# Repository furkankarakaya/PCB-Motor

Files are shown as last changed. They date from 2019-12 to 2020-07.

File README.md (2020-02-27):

# PCB-Motor

* Nominal speed: 2000 RPM

* Nominal torque: 180 mN.m

* Nominal output power: 38 W

* Pole: 16

* Frequency: 266.67 Hz

* Iphase: 2 Arms

* Core width: 5 mm

* Core inner diameter: 50 mm

* Core outer diameter: 92 mm

* Magnet width: 2 mm

* Air gap: 1 mm

* PCB width: 1 mm

* PCB inner diameter: 50 mm

* PCB outer diameter: 98 mm

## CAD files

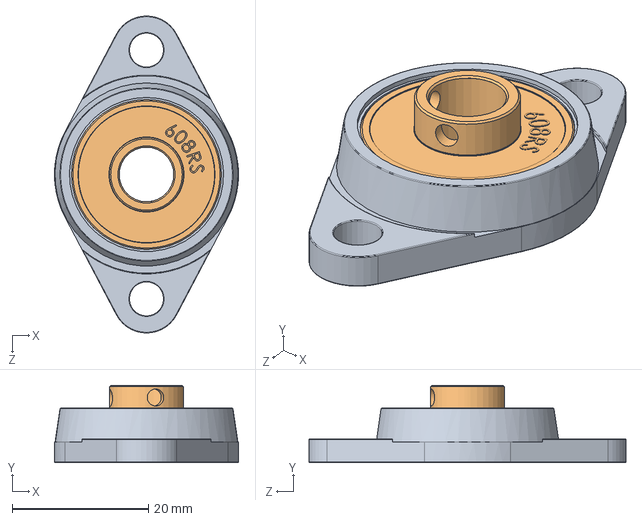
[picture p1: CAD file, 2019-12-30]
mechanical model/ufl-serisi-yatakli-rulman-ufl-series-bearing-1.snapshot.3/KFL08.SLDASM
27.0 x 11.4 x 46.5 mm
KFL08
608RS

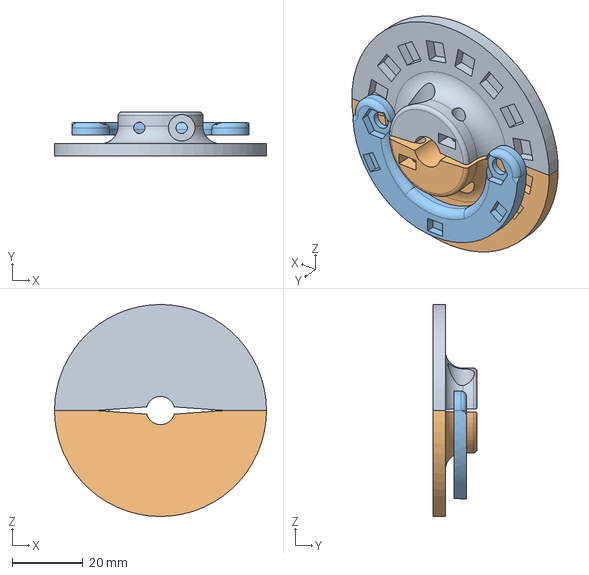
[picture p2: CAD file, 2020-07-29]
mechanical model/hall sensor assembly/PCBmotor-HallSensor.stp
60.0 x 12.5 x 60.0 mm

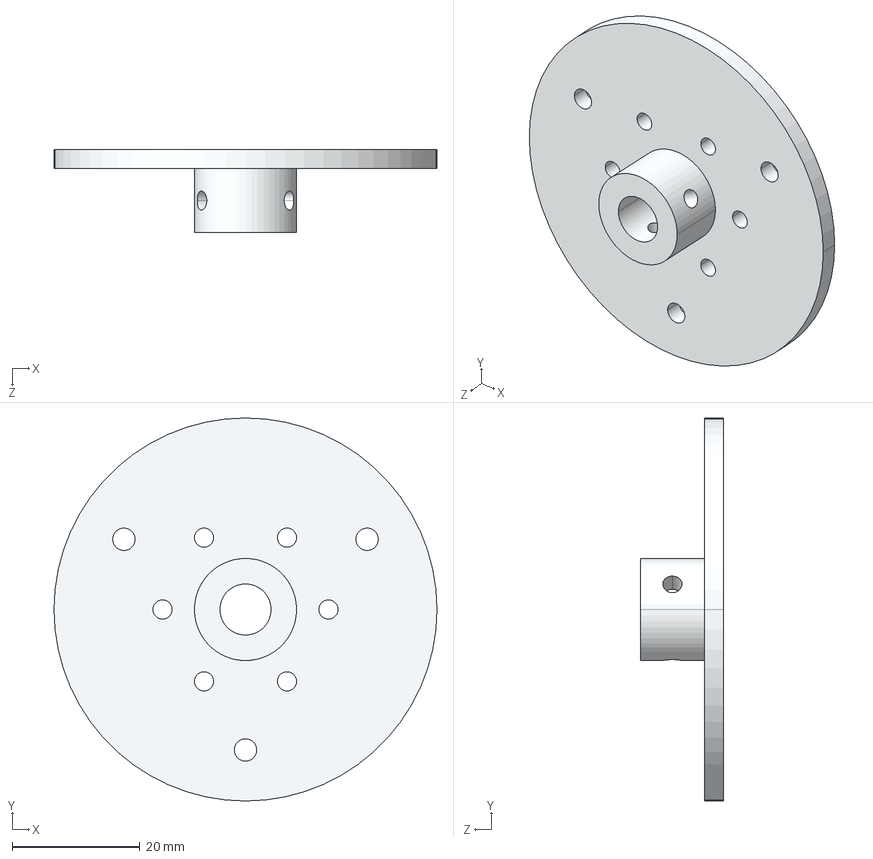
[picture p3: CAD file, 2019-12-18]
mechanical model/üretim/yeni_kapak.STEP
60.0 x 60.0 x 13.0 mm

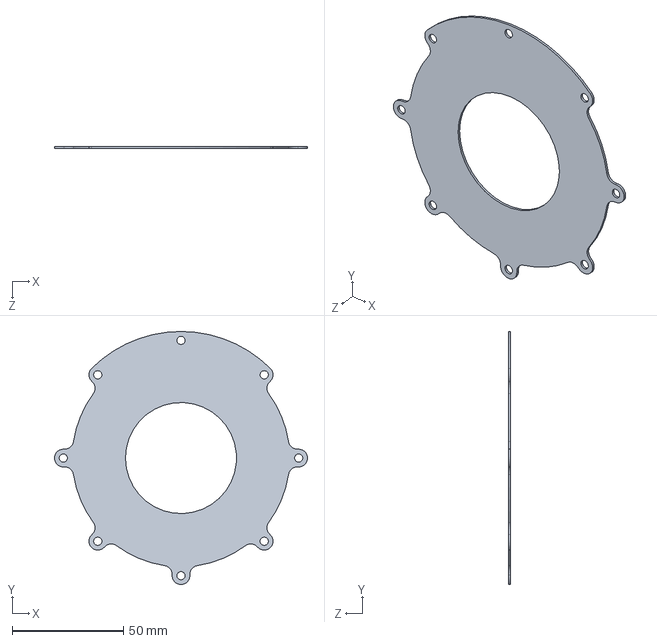
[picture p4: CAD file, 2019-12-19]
pcb/mechanical outline/outline.SLDPRT
113.9 x 114.0 x 1.00 mm

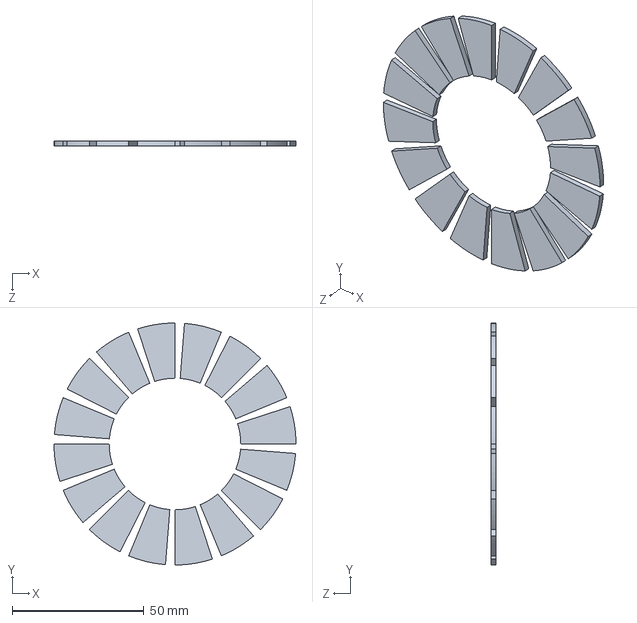
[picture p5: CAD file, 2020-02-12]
mechanical model/Magnets.SLDPRT
92.0 x 92.0 x 2.00 mm

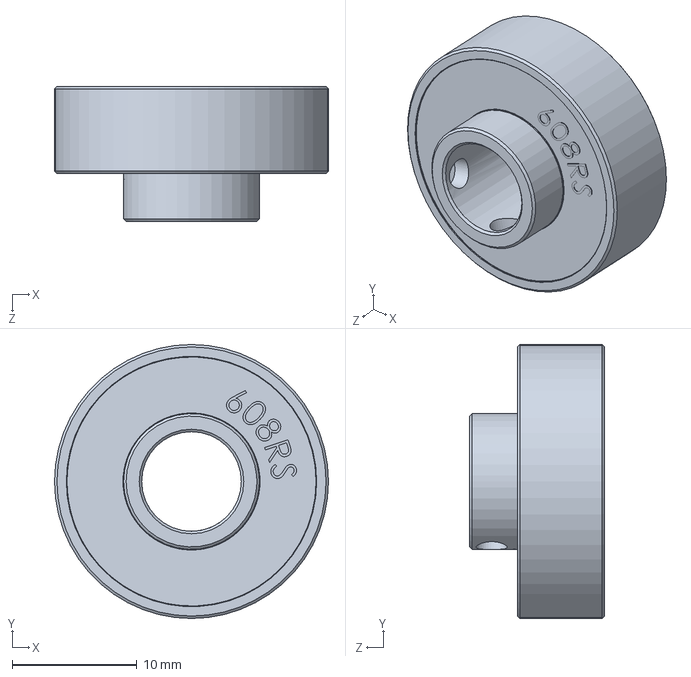
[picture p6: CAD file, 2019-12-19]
mechanical model/ufl-serisi-yatakli-rulman-ufl-series-bearing-1.snapshot.3/608RS.SLDPRT
22.0 x 22.0 x 10.9 mm

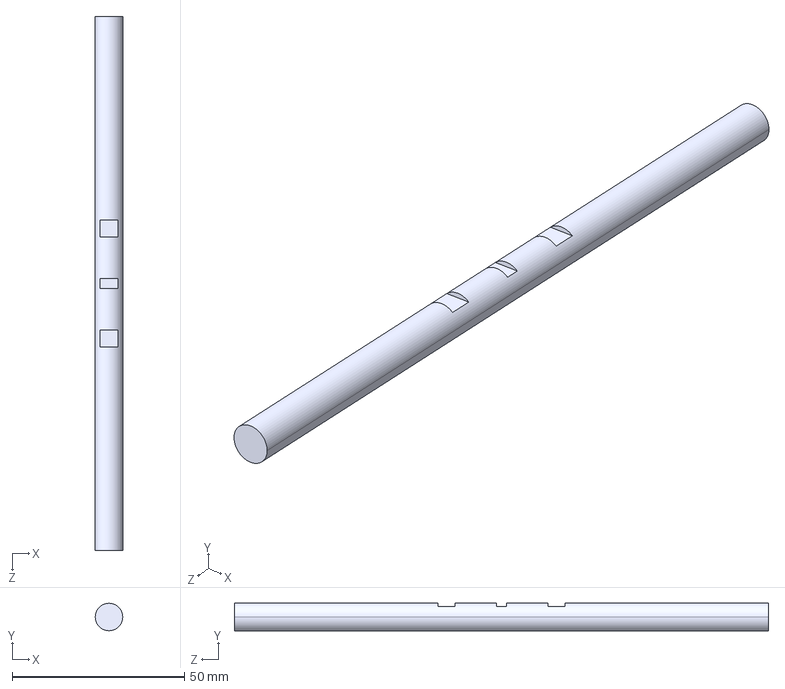
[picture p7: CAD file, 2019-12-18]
mechanical model/üretim/yeni_mil.STEP
8.00 x 8.00 x 155.0 mm

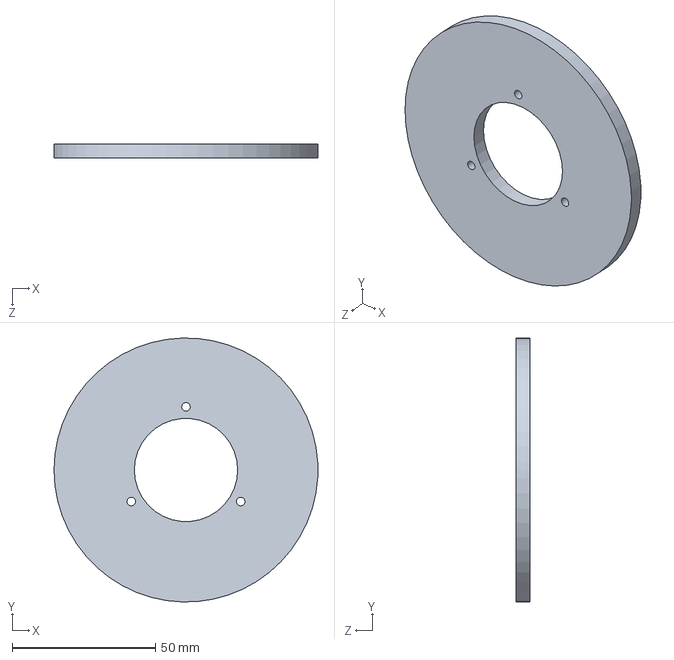
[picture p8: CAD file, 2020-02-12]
mechanical model/rotor.SLDPRT
92.0 x 92.0 x 5.00 mm

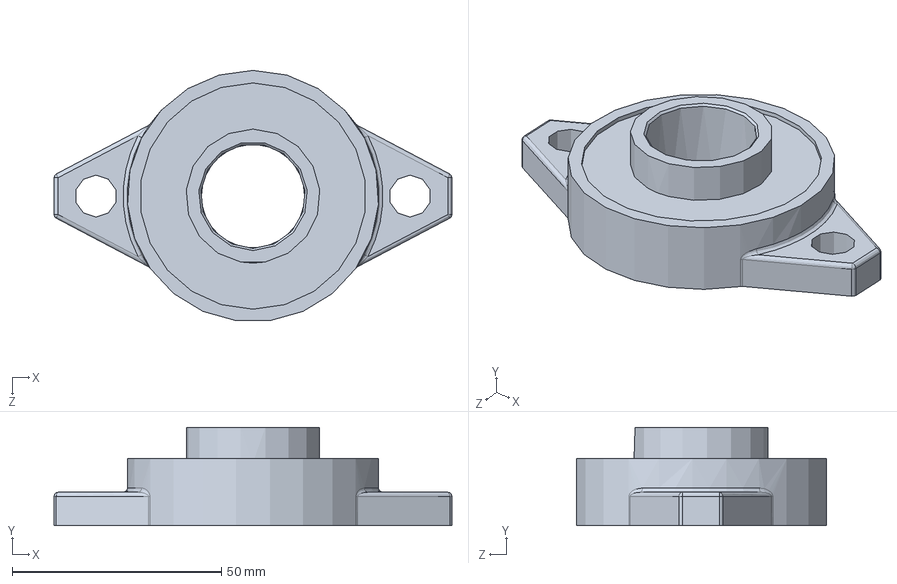
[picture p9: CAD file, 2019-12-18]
mechanical model/ufl-serisi-yatakli-rulman-ufl-series-bearing-1.snapshot.3/Yatakli Rulman UFL.SLDPRT
95.0 x 23.5 x 59.7 mm

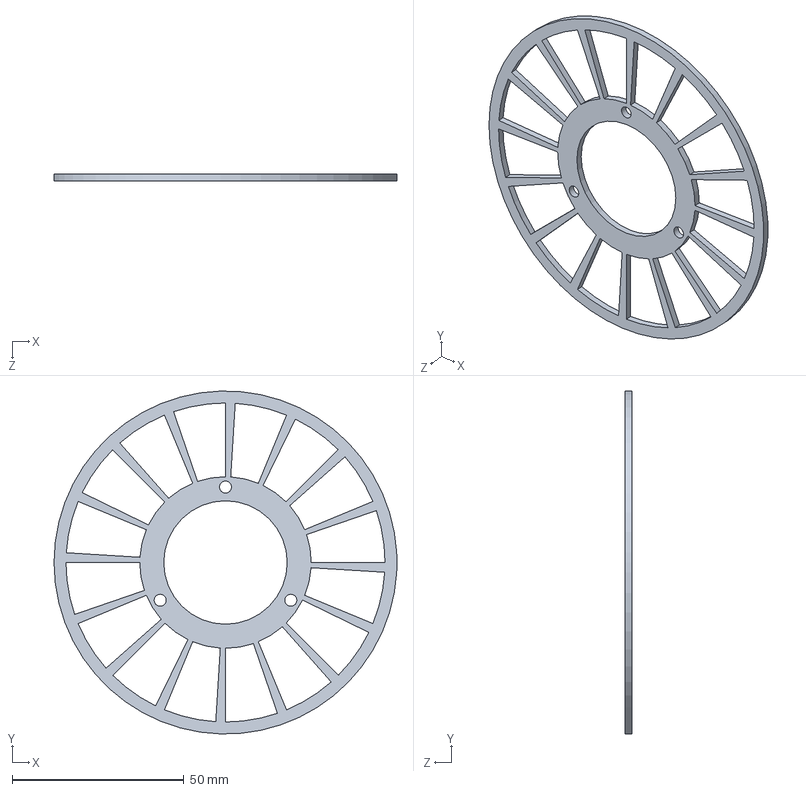
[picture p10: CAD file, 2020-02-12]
mechanical model/magnet tutucu.SLDPRT
100.0 x 100.0 x 2.00 mm

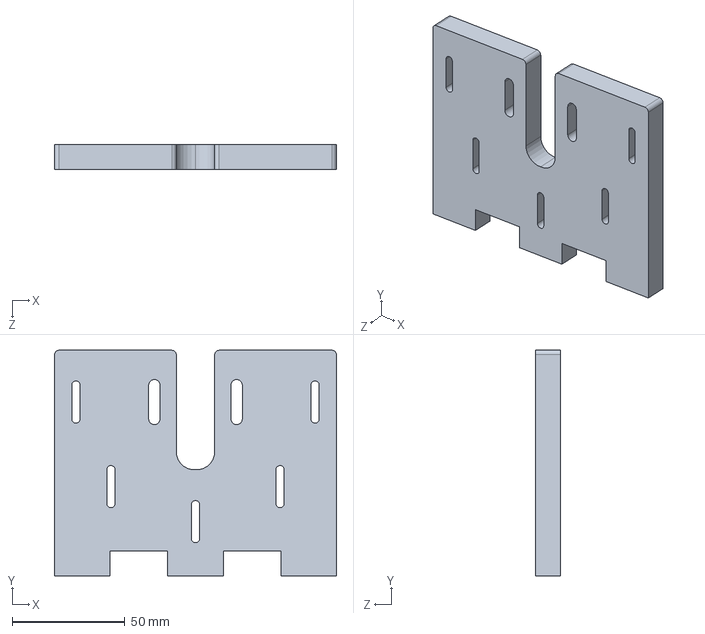
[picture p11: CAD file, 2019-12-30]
mechanical model/yan_destek.SLDPRT
125.0 x 100.0 x 11.0 mm

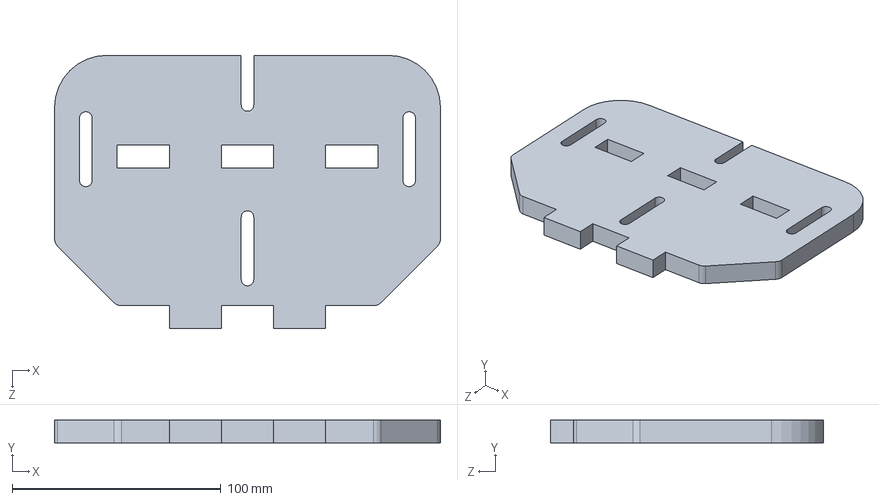
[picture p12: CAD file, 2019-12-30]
mechanical model/alt_destek.SLDPRT
185.0 x 11.0 x 131.0 mm

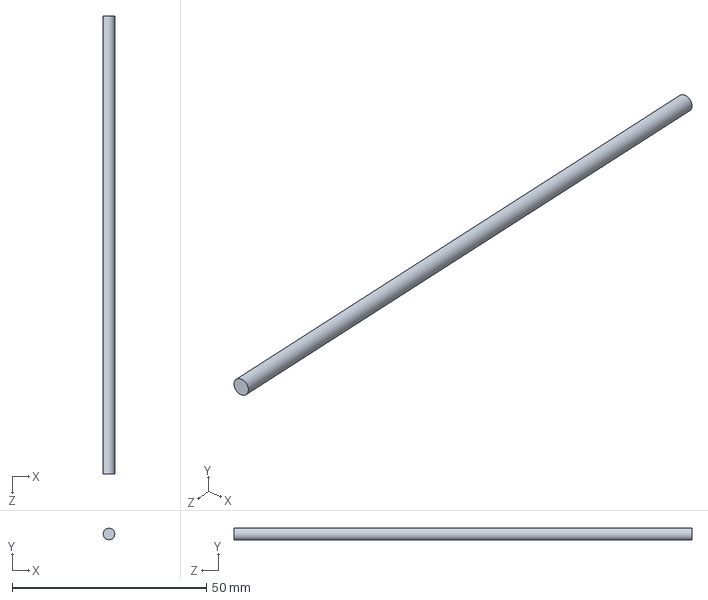
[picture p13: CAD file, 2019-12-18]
mechanical model/saplama.SLDPRT
3.00 x 3.00 x 118.0 mm

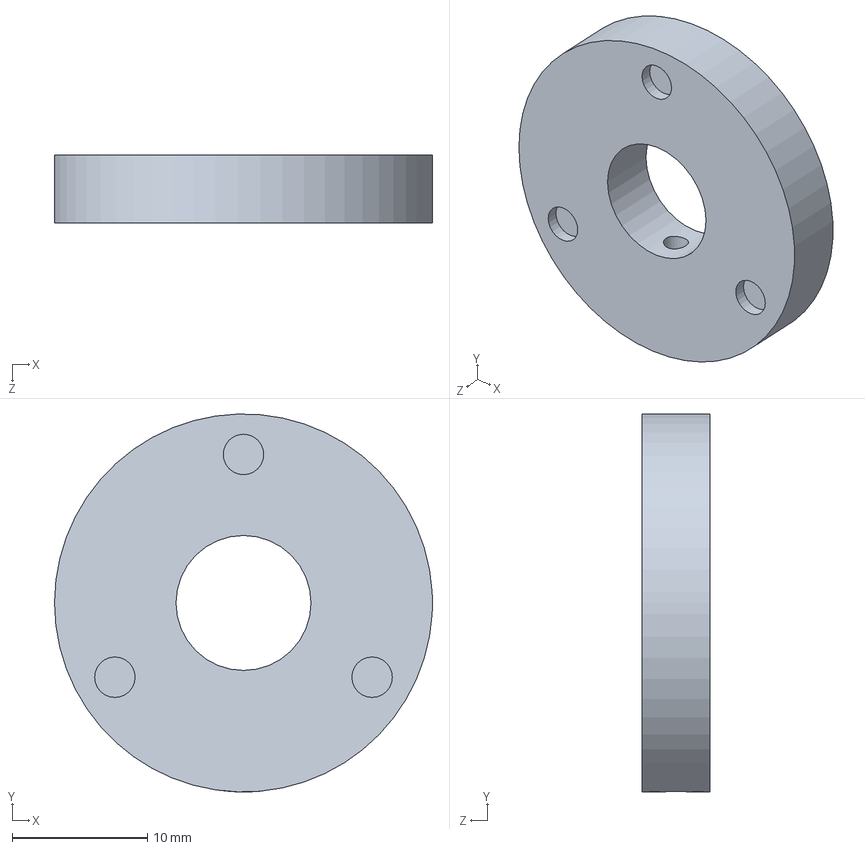
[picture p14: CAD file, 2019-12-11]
mechanical model/dayanak.SLDPRT
28.0 x 28.0 x 5.00 mm

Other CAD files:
mechanical model/wave_winding.SLDPRT
mechanical model/üretim/rotor.STEP
mechanical model/mil.SLDPRT
mechanical model/kapak.SLDPRT
mechanical model/hall sensor assembly/PCBmotor-HallSensor.f3d
mechanical model/hall sensor assembly/PCBmotor-HallSensor.stl
mechanical model/pcb.SLDPRT
mechanical model/rotor-kaburgali.SLDPRT
mechanical model/ufl-serisi-yatakli-rulman-ufl-series-bearing-1.snapshot.3/KFL08.SLDPRT
mechanical model/üretim/rotor.SLDDRW

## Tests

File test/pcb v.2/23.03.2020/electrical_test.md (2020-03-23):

# Electrical test of the PCB
## Concentric Winding
### Phase A
- 1.07 Ohm
- 10.4 uH

### Phase B
- 1.07 Ohm
- 10.4 uH

### Phase C
- 1.07 Ohm
- 10.4 uH

## Parallel Winding
### Phase A
- 789 mOhm
- 3.15 uH

### Phase B
- 787 mOhm
- 3.13 uH

### Phase C
- 806 mOhm
- 3.17 uH

## ARC Winding
### Phase A
- 896 mOhm
- 3.34 uH

### Phase B
- 894 mOhm
- 3.34 uH

### Phase C
- 914 mOhm
- 3.35 uH

## UEW Winding
### Phase A
- 661 mOhm
- 3 uH

### Phase B
- 661 mOhm
- 3 uH

### Phase C
- 679 mOhm
- 3.05 uH

## Radial Winding
### Phase A
- 860 mOhm
- 4 uH

### Phase B
- 859 mOhm
- 4 uH

### Phase C
- 877 mOhm
- 4 uH

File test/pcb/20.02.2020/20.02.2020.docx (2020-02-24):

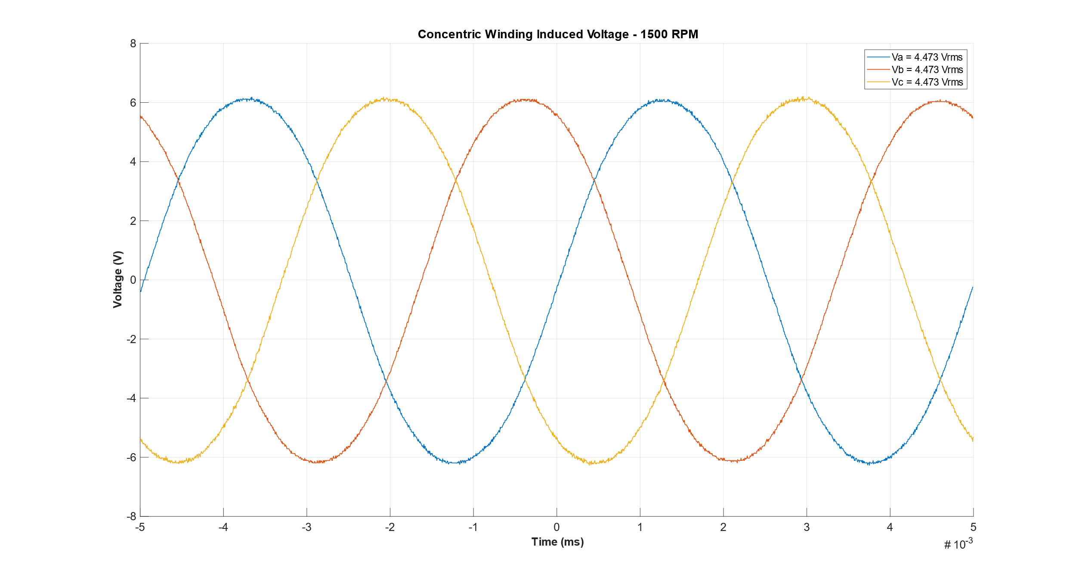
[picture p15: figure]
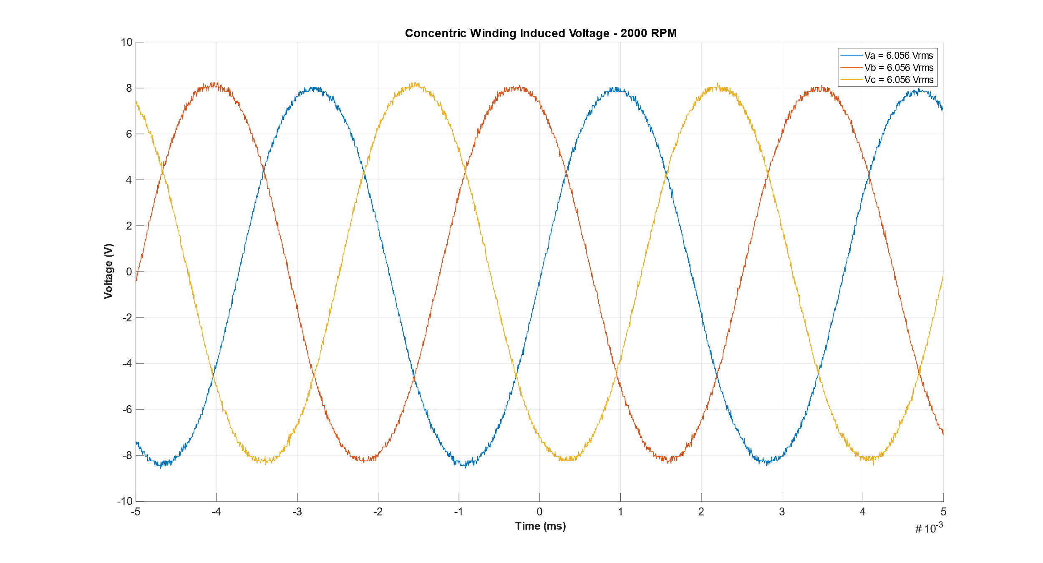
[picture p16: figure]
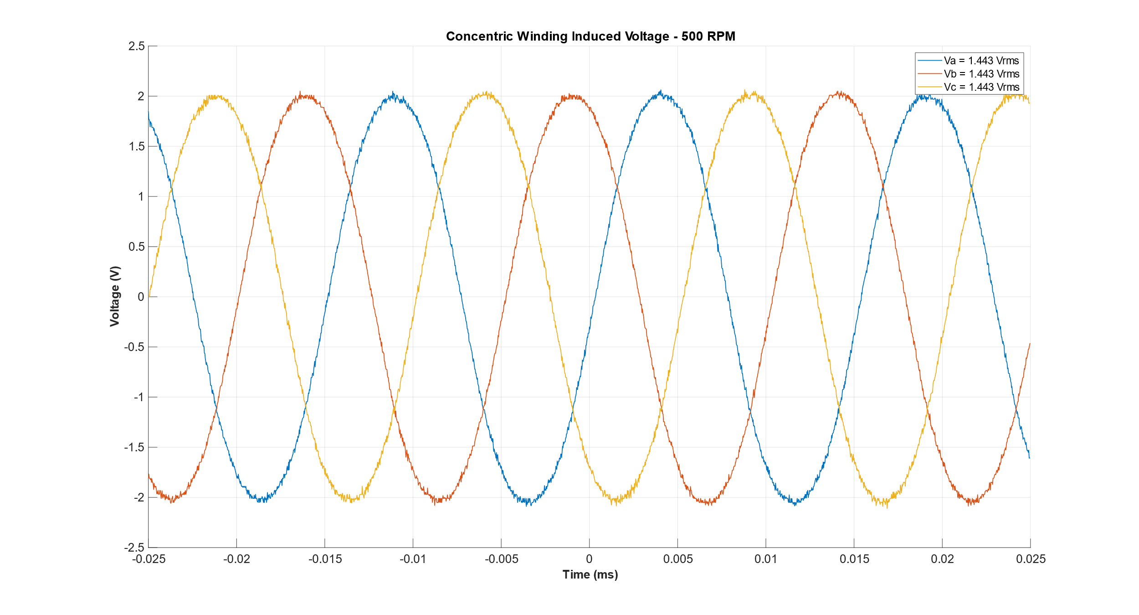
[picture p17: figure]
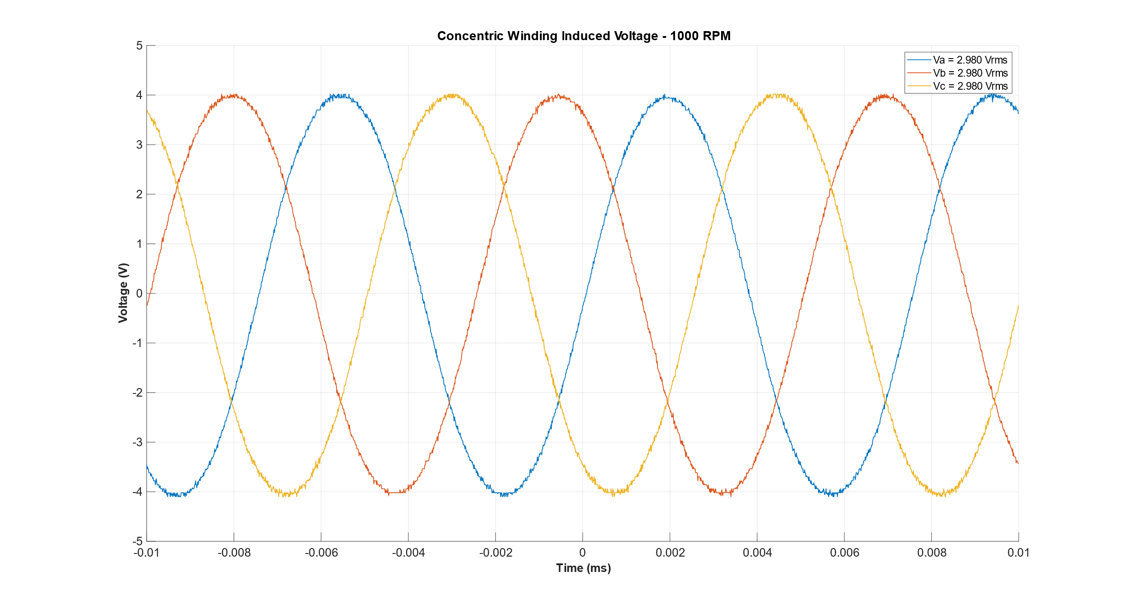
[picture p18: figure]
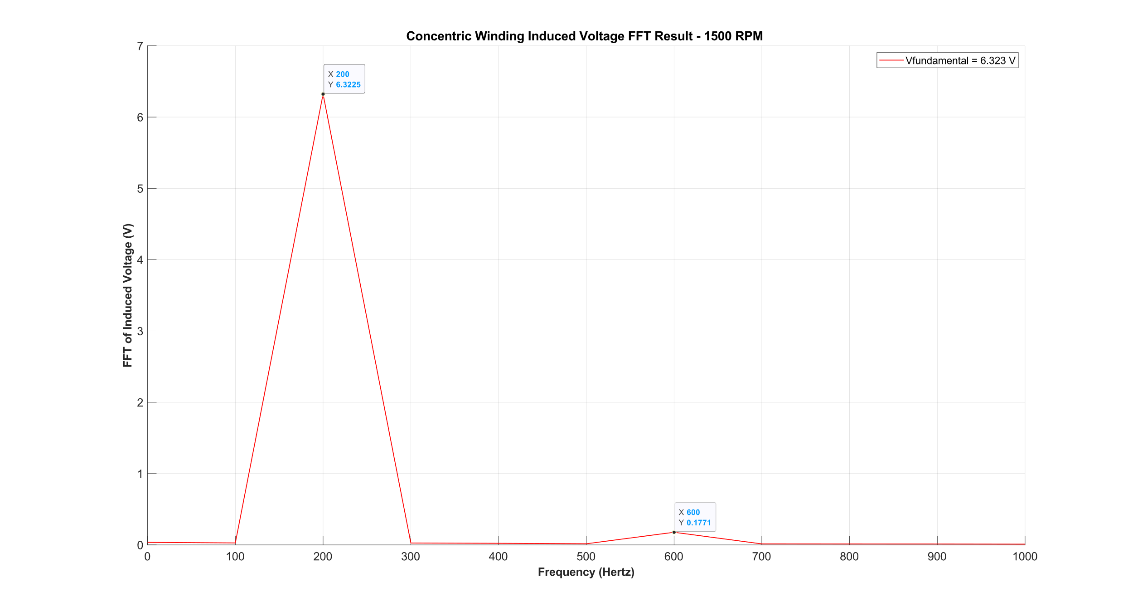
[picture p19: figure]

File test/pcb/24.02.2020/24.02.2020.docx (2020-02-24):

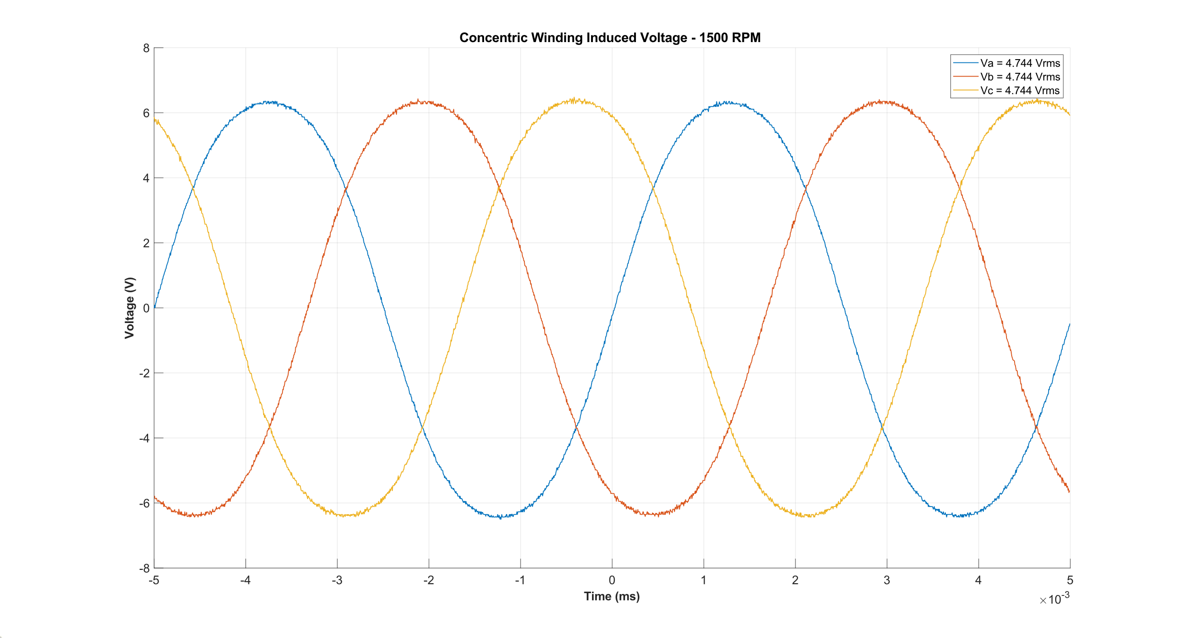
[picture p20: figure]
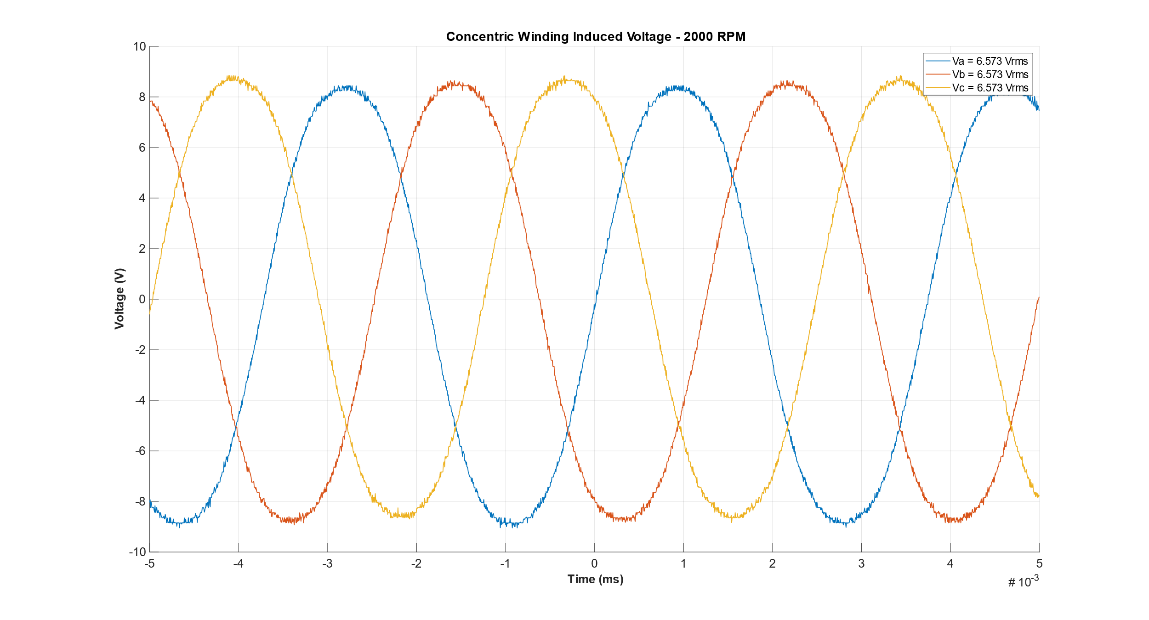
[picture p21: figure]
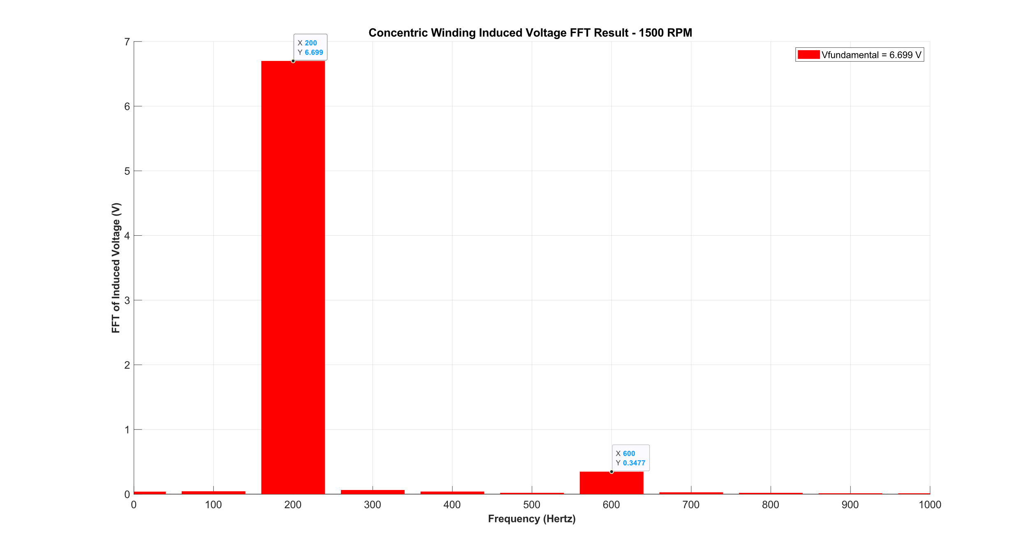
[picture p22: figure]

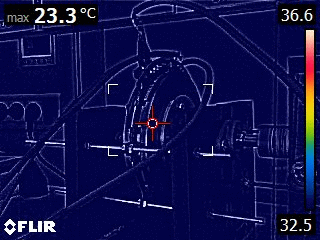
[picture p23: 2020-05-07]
test/pcb v.2/08.04.2020/radial.gif

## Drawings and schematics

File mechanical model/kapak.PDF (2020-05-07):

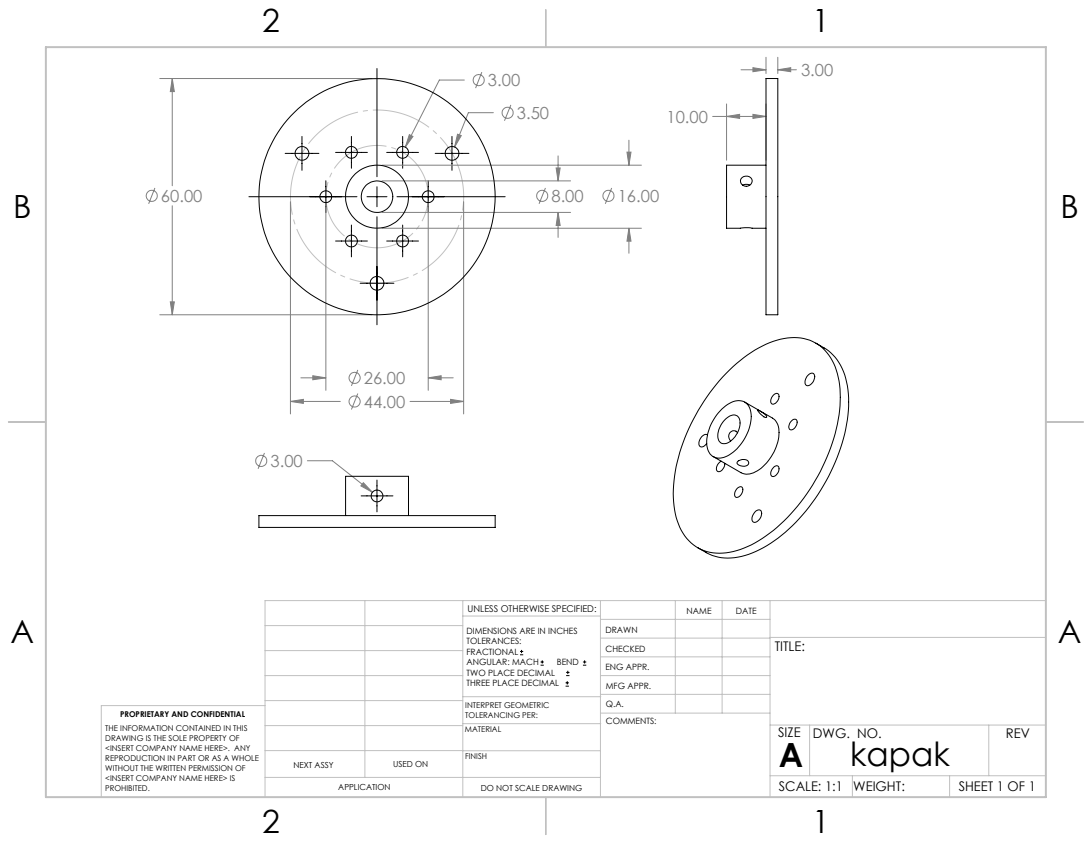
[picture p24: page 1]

UNLESS OTHERWISE SPECIFIED: | | NAME | DATE
DIMENSIONS ARE IN INCHES TOLERANCES: FRACTIONAL ANGULAR: MACH BEND TWO PLACE DECIMAL THREE PLACE DECIMAL | DRAWN

CHECKED | | | TITLE:

ENG APPR.
MFG APPR.

INTERPRET GEOMETRIC TOLERANCING PER: | Q.A.
MATERIAL | | SIZE A | DWG. NO. kapak | REV

PROPRIETARY AND CONFIDENTIAL
THE INFORMATION CONTAINED IN THIS
DRAWING IS THE SOLE PROPERTY OF
<INSERT COMPANY NAME HERE>. ANY
REPRODUCTION IN PART OR AS A WHOLE
WITHOUT THE WRITTEN PERMISSION OF
<INSERT COMPANY NAME HERE> IS
PROHIBITED.

NEXT ASSY | USED ON | FINISH

APPLICATION | DO NOT SCALE DRAWING | | SCALE: 1:1 | WEIGHT: | SHEET 1 OF 1

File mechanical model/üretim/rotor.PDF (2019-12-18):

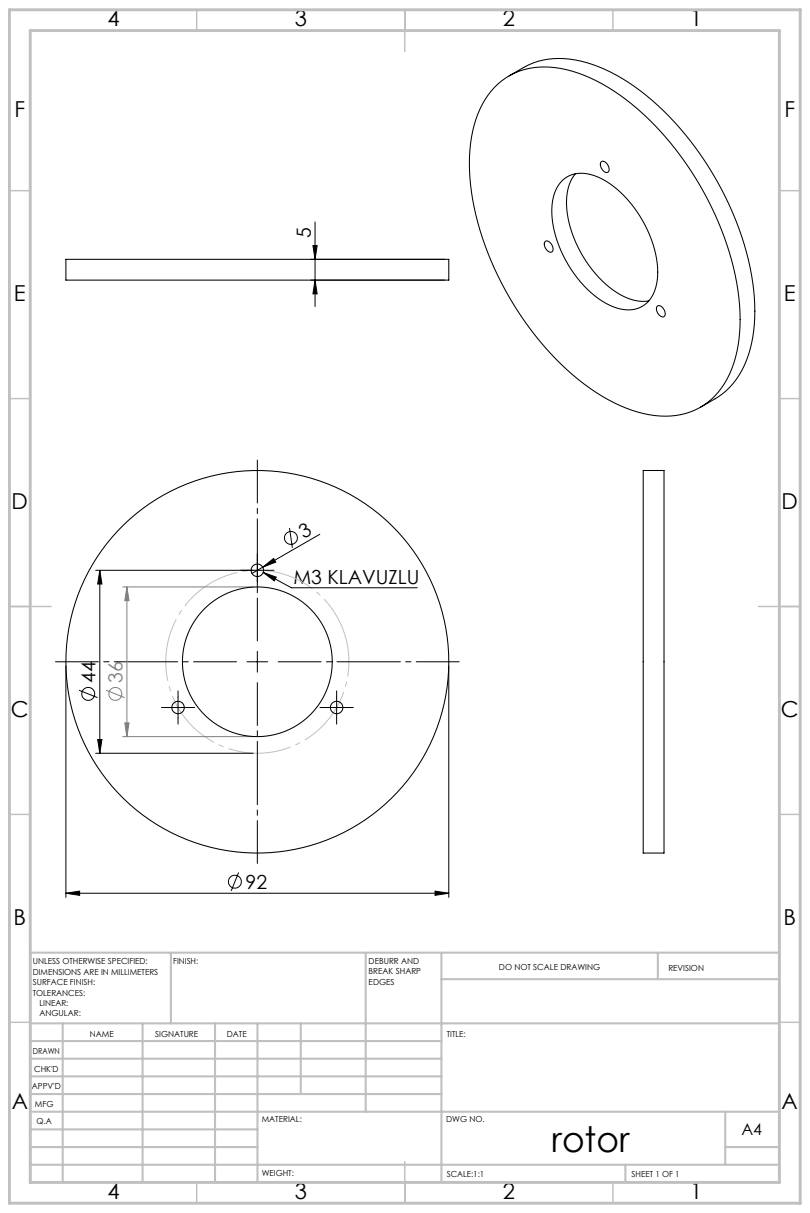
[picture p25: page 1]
M3 KLAVUZLU 5; FINISH:; DEBURR AND; BREAK SHARP; DO NOT SCALE DRAWING; REVISION; SCALE:1:1; SHEET 1 OF 1

UNLESS OTHERWISE SPECIFIED:
DIMENSIONS ARE IN MILLIMETERS
SURFACE FINISH:
TOLERANCES:
LINEAR:
ANGULAR:

NAME | SIGNATURE | DATE | | | | TITLE:

DRAWN
CHK'D
APPV'D
MFG
Q.A | | | | MATERIAL: | DWG NO. rotor | A4

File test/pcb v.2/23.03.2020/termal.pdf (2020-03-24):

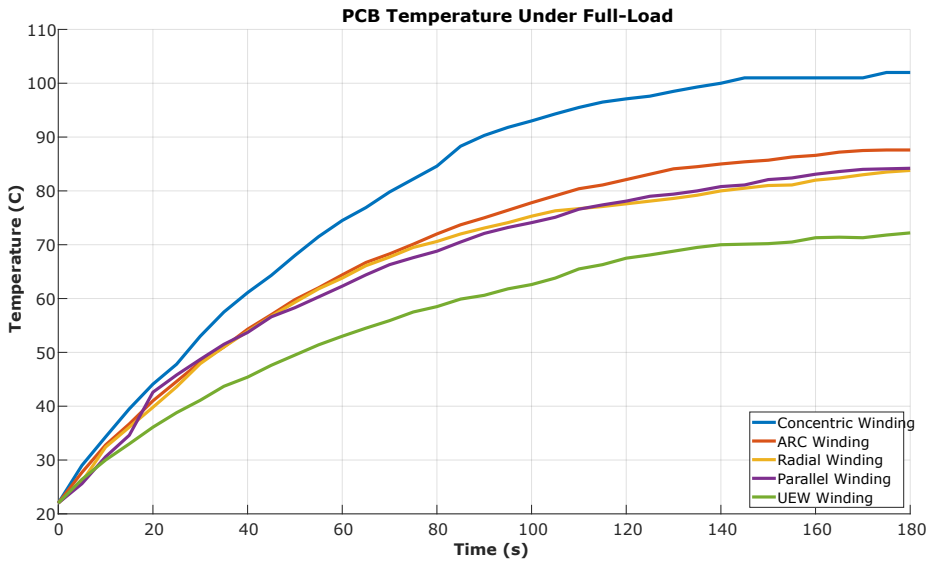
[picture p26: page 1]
Time (s); Temperature (C); Concentric Winding

PCB Temperature Under Full-Load

ARC Winding Radial Winding

Parallel Winding UEW Winding

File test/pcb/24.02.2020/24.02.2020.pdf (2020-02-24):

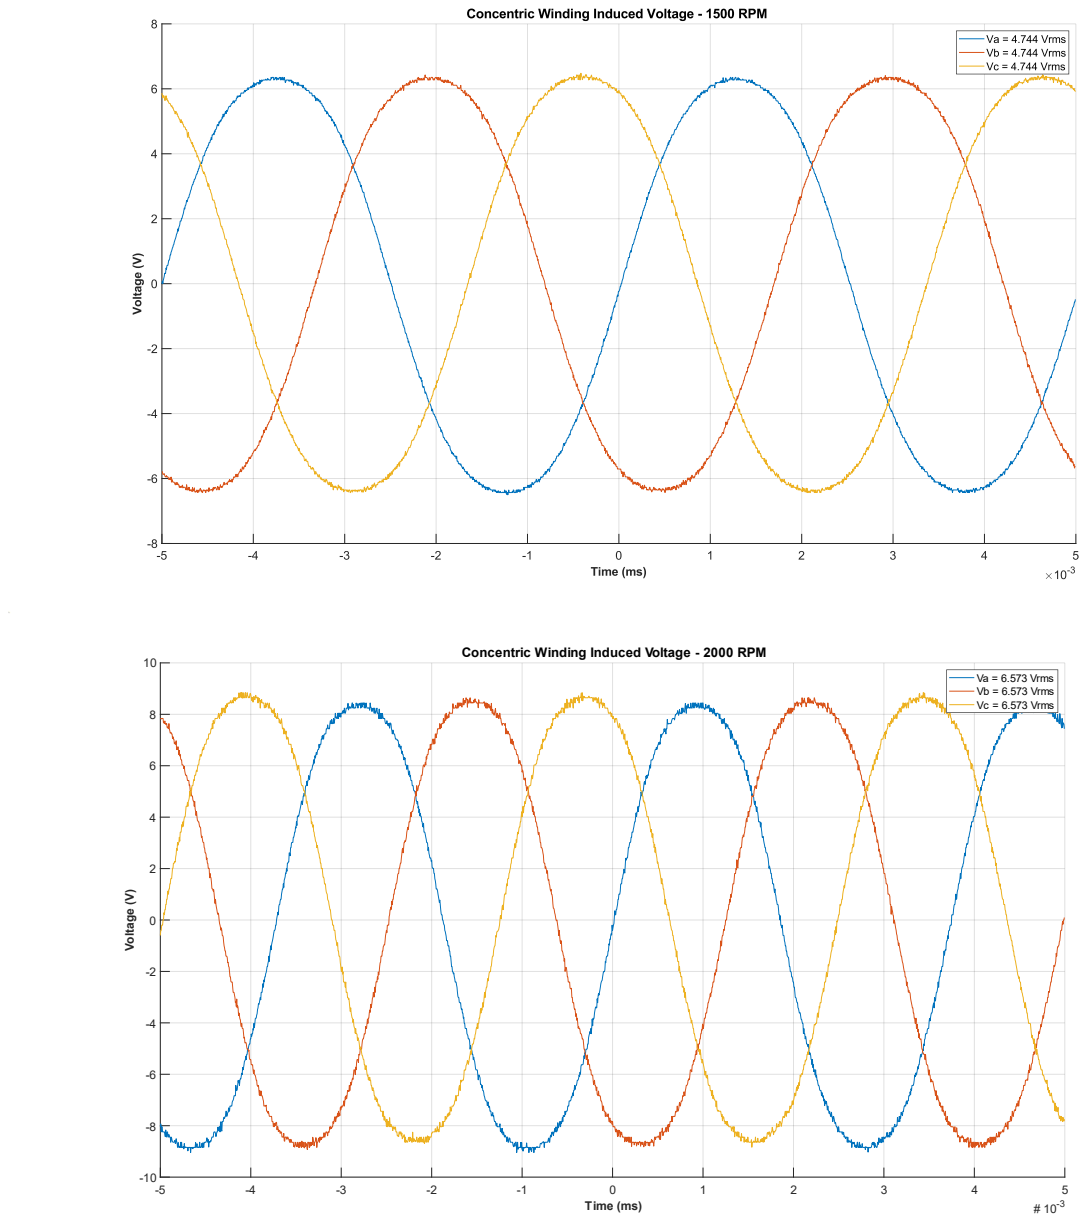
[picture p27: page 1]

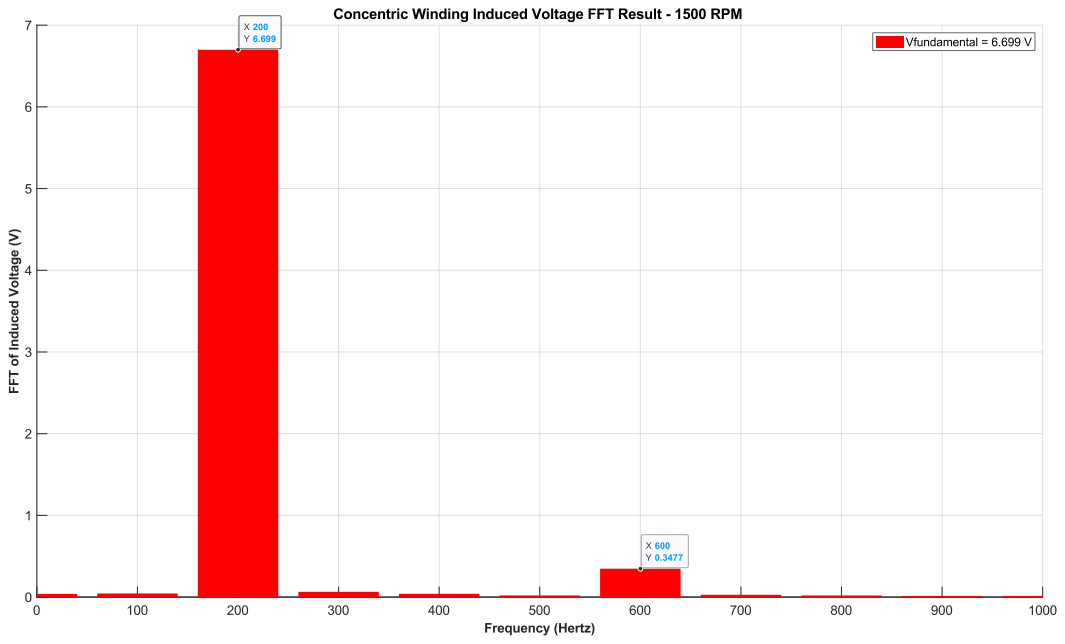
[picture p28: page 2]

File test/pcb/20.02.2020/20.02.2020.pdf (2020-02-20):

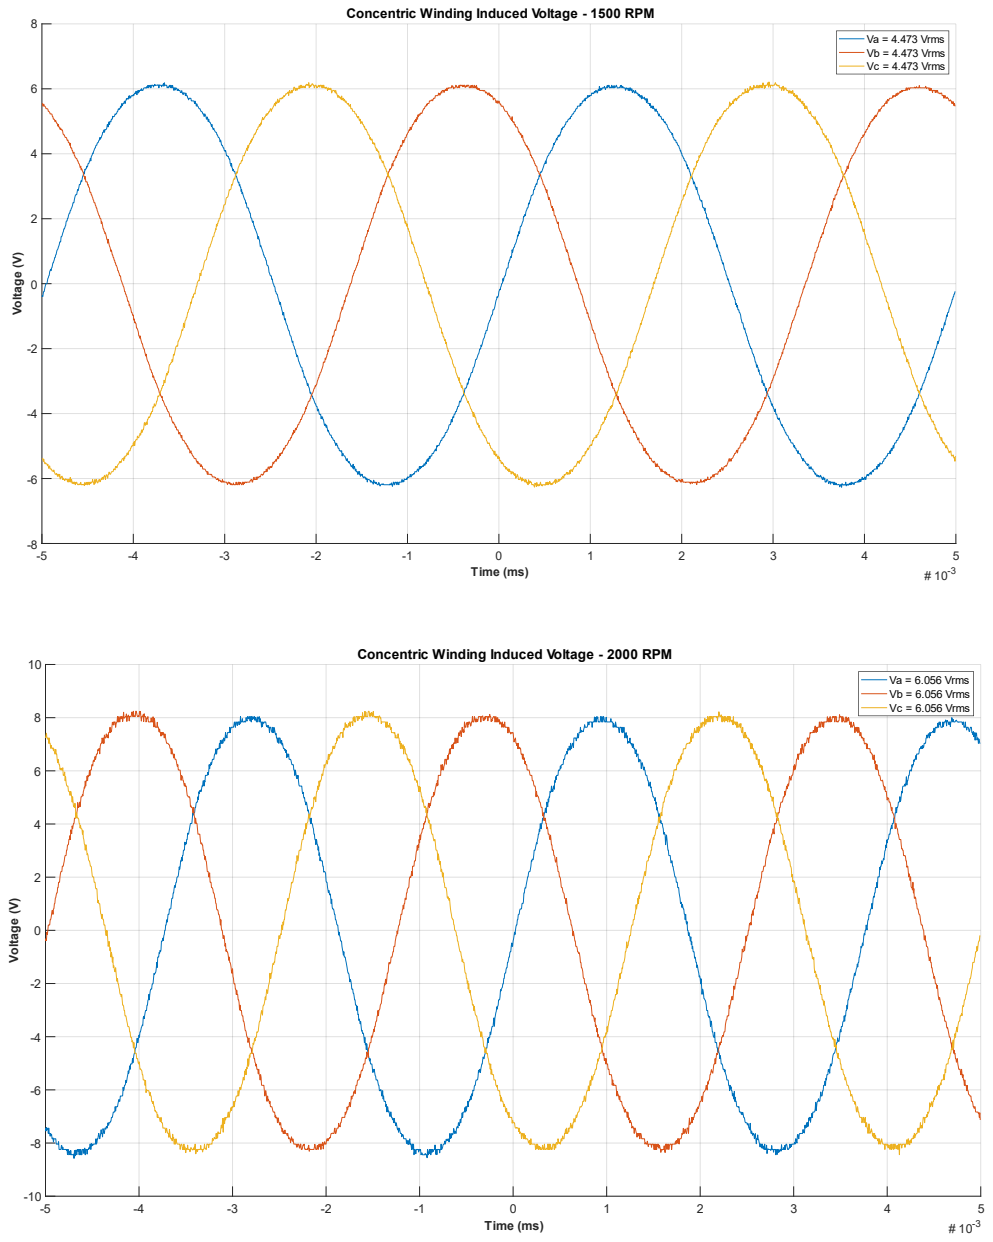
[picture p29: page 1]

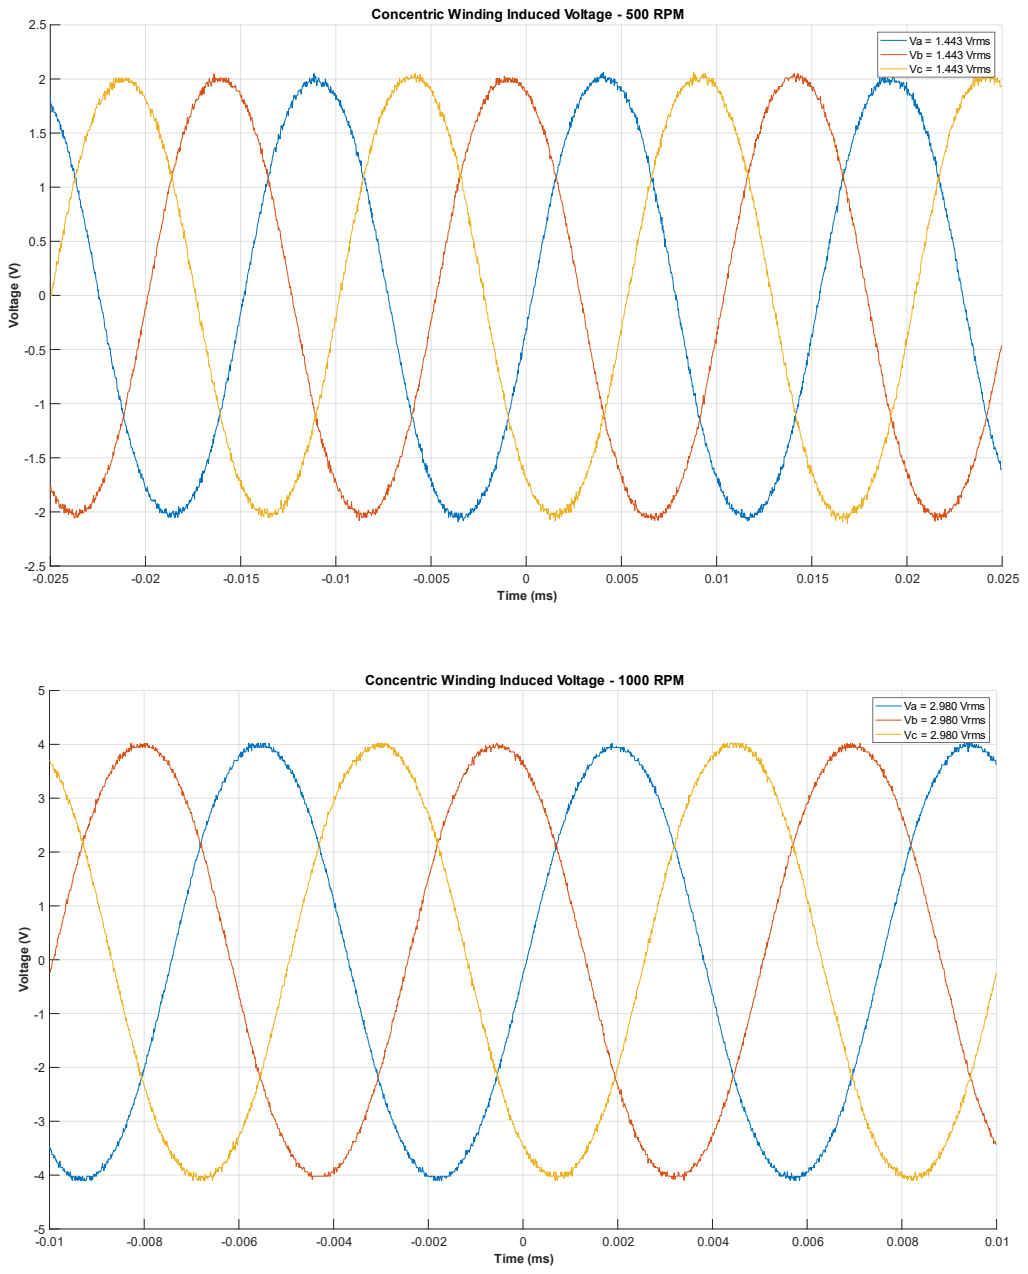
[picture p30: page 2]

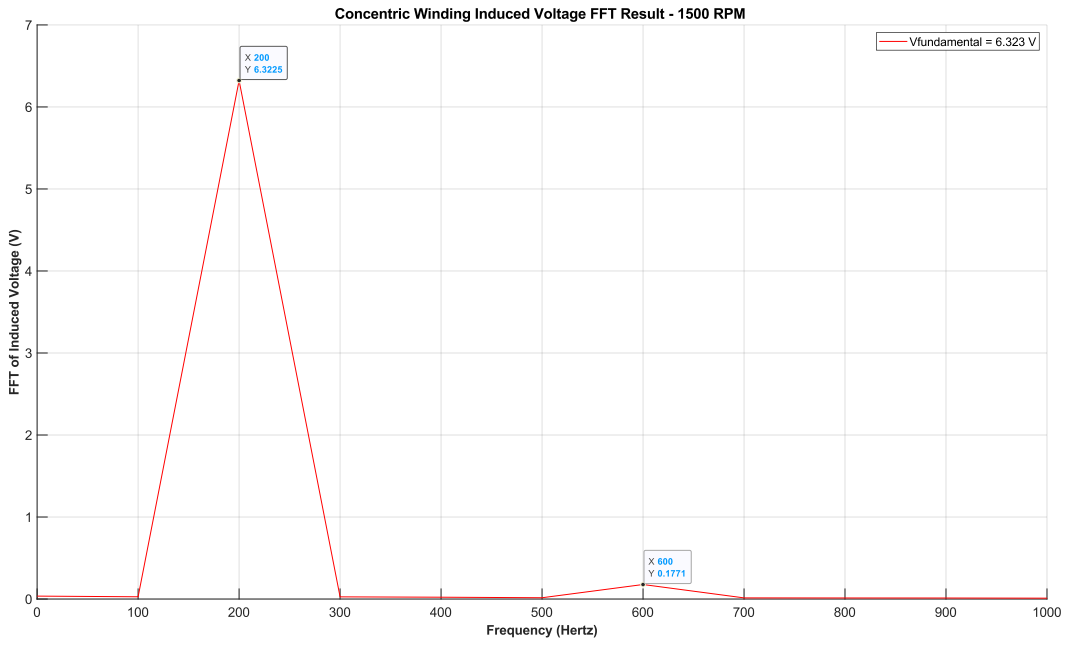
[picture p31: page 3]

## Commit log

2019-10-17 mesh noise problemi çözüldü. 1 oz pcb denenecek.
2019-10-24 sarmal tasarım pcb
    [2Layer2Oz.PcbDoc, outline.SLDPRT]
2019-10-24 pcb motor 2 layer 2 oz pcb çizildi.
    [2Layer2Oz.PcbDoc, PCB_Motor.PcbDoc, outline.SLDPRT]
2019-10-25 pcb üretime gönderildi. maxwell analizi yapılıyor.
    [PCB_Motor.PcbDoc]
2019-10-30 PCB güncellendi. Labeling, versiyon-yıl eklendi. Top soldermask kaldırıldı.
    [PCB_Motor.PcbDoc]
2019-11-22 thermal test of the pcb is completed
2019-12-04 double sided analytical calculation added
    [double_sided.xlsx]
2019-12-04 mechanical model is added
    [Yatakli Rulman UFL.SLDPRT, assembly.SLDASM, sabitleme.SLDPRT]
2019-12-10 mechanical models are added
    [Magnets.SLDPRT, assembly.SLDASM, dayanak.SLDPRT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]
2019-12-10 sabitleme küçültüldü
    [alt_tabla.SLDPRT, assembly.SLDASM, sabitleme.SLDPRT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]
2019-12-10 genel tasarım hazır
    [alt_destek.SLDPRT, alt_tabla.SLDPRT, assembly.SLDASM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]
2019-12-11 mechanical model is completed.
    [Magnets.SLDPRT, alt_destek.SLDPRT, assembly.SLDASM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]
2019-12-18 dayanak kaldırıldı, kapak değiştirildi
    [alt_destek.SLDPRT, assembly.SLDASM, kapak.SLDPRT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]
2019-12-18 ÜRETİM DÖKÜMANLARI
    [Magnets.SLDPRT, Yatakli Rulman UFL.SLDPRT, al_ilk_sac_kesim.DWG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]
2019-12-18 8 mm mil eklendi
    [assembly.SLDASM, kapak.SLDPRT, mil.SLDPRT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]
2019-12-19 8 mm mile göre dizayn değiştirildi. sabitleme aparatı düzeltildi.
    [608RS.SLDPRT, KFL08.SLDASM, KFL08.SLDPRT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]
2019-12-30 ufak değişiklikler
    [KFL08.SLDASM, alt_destek.SLDPRT, assembly.SLDASM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]
2020-02-05 ilk wave winding tasarımı tamamlandı
    [PCB_Motor.PcbDoc, double_sided.xlsx, double_sided_1500.xlsx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]
2020-02-07 farklı winding denemeleri ve fea
    [arc.PcbDoc, concentric.PcbDoc, overlapping_parallel.PcbDoc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]
2020-02-10 wave winding pcbleri çizildi, concentric için harmonik analiz yapıldı.
    [PCB_Motor.PcbDoc, UEW_overlapping_parallel.PcbDoc, arc.PcbDoc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]
2020-02-12 fea modelleri oluşturulmaya başlandı
    [Magnets.SLDPRT, UEW_overlapping_parallel.PcbDoc, arc.PcbDoc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]
2020-02-15 clearence 8 mile çıkarıldı. fea modelleri beklendiği gibi çalışıyor.
    [UEW_overlapping_parallel.PcbDoc, arc.PcbDoc, concentric.PcbDoc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]
2020-02-27 2000 rpm eklendi
2020-02-28 optimization code is updated.
    [airgap.csv]
2020-03-24 thermal and electrical tests are conducted
    [poligon alanı hesaplamaca.xlsx]
2020-03-25 magnetic scalar potential is used to calculate b field. results are compared with FEA
2020-03-30 induced voltage calculation trials
2020-04-02 harmonics are added to induced voltage leakage problem
2020-04-03 radial winding induced voltage calculations is completed. parallel winding torque is calculated.
2020-05-05 induced voltage calculations are improved by r dependent term
2020-05-07 repo bahar temizliği
    [608RS.SLDPRT, KFL08.SLDASM, KFL08.SLDPRT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]
2020-05-07 directory düzeltme
    [UEW_overlapping_parallel.PcbDoc, arc - Copy.PcbDoc, arc.PcbDoc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]
2020-07-29 Hall effect sensörü modelleri yüklendi
    Test düzeneği üzerine monte edilen sensör parçaları.
    [PCBmotor-HallSensor.f3d, PCBmotor-HallSensor.stl, PCBmotor-HallSensor.stp]
